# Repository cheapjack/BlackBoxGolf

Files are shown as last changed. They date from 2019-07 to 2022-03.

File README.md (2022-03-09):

# Black Box Golf
Make files, instructions and details of a Science & Technology Studies Crazy Golf hole for [Full Of Noises 2019](http://fonfestival.org/event/full-of-noises-2019-09-11-08-19/) in Barrow Park, Barrow-in-Furness

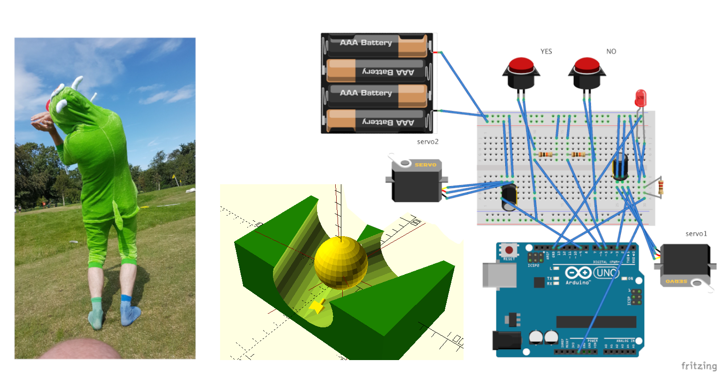
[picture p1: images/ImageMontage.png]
Participant dressed as Euglena, Fritzing Model and 3D CAD for internals


## Premise

Black Boxing is where a very complicated technology (like a computer or a bank) effectively becomes a box hiding how it really works: all we know as black box users is we put something in and expect something to come out. Most of the things we use every day can be seen like this. We thought it would be fun to think about a black box on a golf course.

Science studies is a really useful way of thinking about how science affects society. In Barrow in Furness we can see many ways that science affects our social world; BAE relies on some of the more problematic of scientific developments (weapons & defence) but has a big affect on the local socio-economic world, while many coastal and agricultural sciences have a big role in the town through local industry and agriculture. 

To cite Science Studies scholar Bruno Latour, blackboxing is *"the way scientific and technical work is made invisible by its own success. When a machine runs efficiently, when a matter of fact is settled, one need focus only on its inputs and outputs and not on its internal complexity. Thus, paradoxically, the more science and technology succeed, the more opaque and obscure they become."* <sup>1</sup> 

It's also good at not just thinking about big global science issues but how things work locally. We wanted to use the golf course as a space to think about how hidden non-human creatures like algae live really close to us, despite living in quite a tightly controlled industrial and agricultural environment. Generally we're too busy surviving in our social worlds to stop and think about tiny creatures, but some family time playing crazy golf might be a nice easy way to think about microbiology. Though of course the important thing is to complete your game in as few shots as possible; and if you follow our black box activity instructions carefully we might help you win and learn about the microscopic world of algae and how scientists use model organisms!

A model organism is a non-human species that is extensively studied to understand particular biological phenomena and provide insight into the workings of other more complicated organisms. Once these things are established in science the model organism is a bit like a black box and scientists use them to test things a bit like we might use a sensor to turn on an outdoor security light.

## What the black box does

A player's ball enters a compartment in an acrylic black box from a short run and is held within the structure and only released after the 'success' or 'failure' of a condition. A 'success' triggers the ball's release down another run advantageous to the player's next hole, while a 'fail', releases the ball somewhere not to the players advantage, ie away from the next hole

The success or fail is triggered by 2 physical buttons that a human judge can operate. It is arduino based and will run from a rechargeable 3V-5V USB battery pack

Players act out instructions provided on the box on the day, that fellow players, friends or family judge whether they deserve a `success` or `fail`. They have to be honest or they can cheat; it's up to the players.

The black box can be deployed as a kit for future crazy golf at Barrow Park and the conditional system can change each time.

Like much of the tech we all depend on, this hole promises alot, but ultimately provides very little; obscuring hidden communities of humans and non-humans who maintain the infrastructures they depend on.

***How*** it all works is hidden in the shiny black box and we don't really need to know all the hard work that has gone into it for it to work in our golf game. If you *do* need to know you can find [instructions here](https://github.com/cheapjack/BlackBoxGolf/blob/master/HowToBuild.md)

## Black Box activity

Players judge the true/YES or false/NO button press based on observing algae in specially prepared microfluidic environments on microscope slides using Manu Prakesh's [Foldscopes](https://foldscope.com) made at the [Prakesh Lab](https://web.stanford.edu/group/prakash-lab/cgi-bin/labsite/) for 'frugal science'. It might lead to you dressing up as algae, what we call *"Euglena Cosplay"*

## Euglena Cosplay

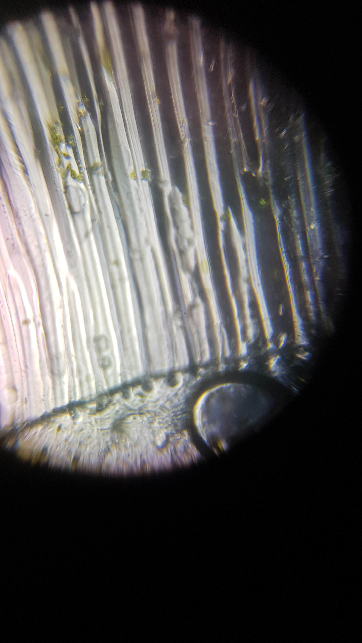
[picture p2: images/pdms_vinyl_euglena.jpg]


Euglena Cosplay is the activity used to self-certify true/YES or false/NO conditions in the black box.

 * Enter golf ball into box
 * Observe Euglena down *Microscope Alley* with pre-prepared [Foldscopes](https://foldscope.com) or failing that on the [model organisms webpage](https://domesticscience.org.uk/criticalkits/euglena.html)
   * They observe Euglena in silicon microfluidic channels moulded from the grooves of Cumbrian charity shop records, a method for model organism observation developed by microbiologist, biotechnologist and engineer [Alexandre Benedetto](https://www.lancaster.ac.uk/health-and-medicine/about-us/people/alexandre-benedetto) inspired by an article in [The Worm Breeders Gazette](http://wbg.wormbook.org/2017/07/18/immobilizing-nematodes-for-live-imaging-using-an-agarose-pad-generated-with-a-vinyl-record/)
    * Wear a Euglena costume and mime their behaviour
    * If you're too embarassed just do mime!
 * Get judged by co-players
 * Hit `true` or `false` buttons
 * Golf ball released:
   * `true`: easy access to next hole
   * `false`: Down a camping stove/ recycled PLA windshield maze

## Cheating

Of course it's up to you to negotiate the complex social world of someone cheating at Crazy Golf; you could choose to do that and ignore our tiny green friends or the brilliant engineerinf behind foldscopes and go straight to a hole-in-one. But you might miss out experiencing some interesting local science techniques.

## How To Build

In quite the opposite spirit to black boxing, read [the basic guide to build it yourself](HowToBuild.md). Arduino abstractions of `C++`, how capacitors, pull up resistors, ground referencing etc work alongwith 300 years of microscopic practice and the physics of ball lenses remain in the black boxes we need them to be in to play this kind of non-human observing crazy golf. 

## References

 * 1. Bruno Latour (1999). Pandora's hope: essays on the reality of science studies. Cambridge, Massachusetts: Harvard University Press. p. 304.

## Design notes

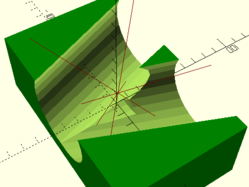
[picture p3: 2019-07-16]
images/Model.png

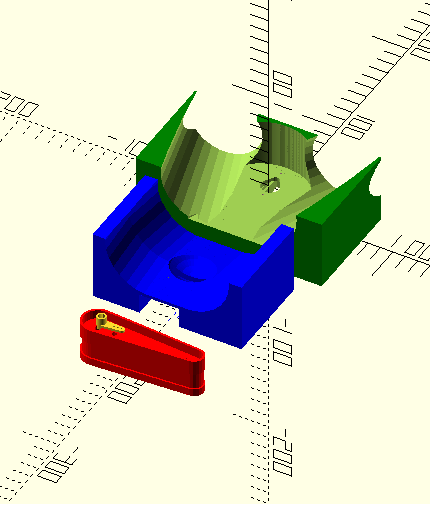
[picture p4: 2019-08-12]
images/model2.png

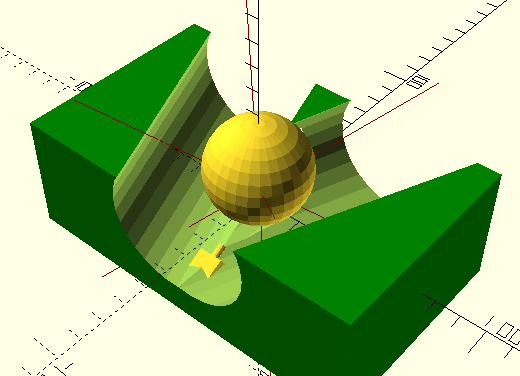
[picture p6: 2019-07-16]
images/blackboxgolfModel.png

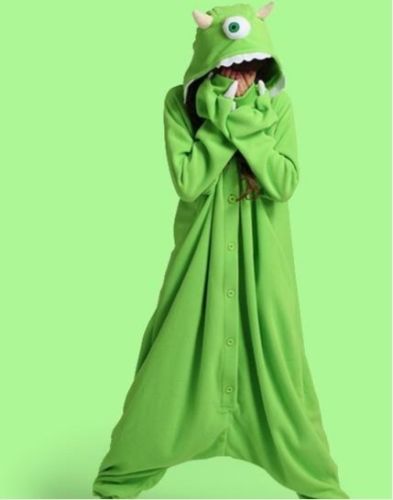
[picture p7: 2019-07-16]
images/mike.jpg

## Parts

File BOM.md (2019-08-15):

### Golf BOM

|No.|Size|Material|Source|Cost(£)|Ordered|Received
|----|----|----|----|----|----|---
1|3-6V|Solenoid|[ebay](#)|4.95|<ul><li>[x] </li>|<ul><li>[x] </li>
2|L/S|Mike Monster<br>Costume|[ebay](#)|35.80|<ul><li>[x] </li>|<ul><li>[x] </li>
2|5V|Hextronik Servo Motors|[ebay](https://www.ebay.co.uk/itm/Hextronik-HXT900-9g-Micro-Servo-1-2-4-Packs-Micro-RC-Planes-Helis-orangeRX-UK/352456068430)|10.99|<ul><li>[x] </li>|<ul><li>[x] </li>
5|2M|Bolt|[ebay](#)||<ul><li>[ ] </li>|<ul><li>[x] </li>
1||Golf Flag|ebay|10.69|<ul><li>[x] </li>|<ul><li>[x] </li>
1||Golf Balls|ebay|12.21|<ul><li>[x] </li>|<ul><li>[x] </li>
1||Folding Camp Deflectors|ebay|10.53|<ul><li>[x] </li>|<ul><li>[x] </li>
1|30ml|Euglena gracilis|[sciento](https://sciento.co.uk)|13.25|<ul><li>[x] </li>|<ul><li>[ ] </li>
1|470uF|Capacitors|amazon|6.99|<ul><li>[x] </li>|<ul><li>[x] </li>
1|UNO|ELEGOO Arduino Compatible R3 Board ATmega328P|[amazon](https://www.amazon.co.uk/gp/product/B01EWOE0UU)|7.99|<ul><li>[x] </li>|<ul><li>[x] </li>
2|AA & AAA|Batteries|Spar Lancaster|6.99|<ul><li>[x] </li>|<ul><li>[x] </li>
20|A5|Instruction Pamphlet|[C3](https://zenithprintgroup.com/c3-imaging/)|20.00|<ul><li>[x] </li>|<ul><li>[x] </li>
1|1000mAh|Solar USB Battery|amazon|18.98|<ul><li>[x] </li>|<ul><li>[ ] </li>
5|600x300mm|Black<br>Acryliv|[Hobarts](https://hobarts.com/3mm-black-cast-acrylic)|42.00|<ul><li>[x] </li>|<ul><li>[x] </li>
||||Total|195.15

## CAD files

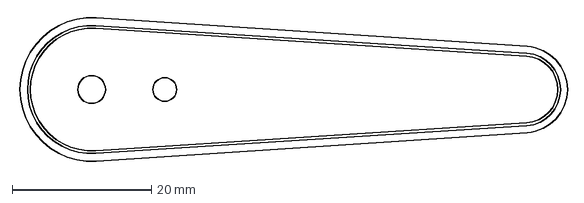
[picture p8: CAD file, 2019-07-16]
builds/flipper/files/flipper_drawings.dxf
79.1 x 21.1 mm

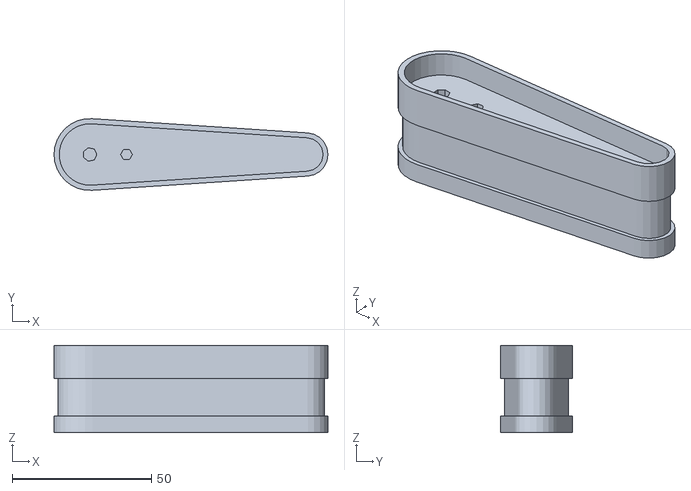
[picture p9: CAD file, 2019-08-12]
builds/Golf_Flipper.stl
98.2 x 25.7 x 31.2

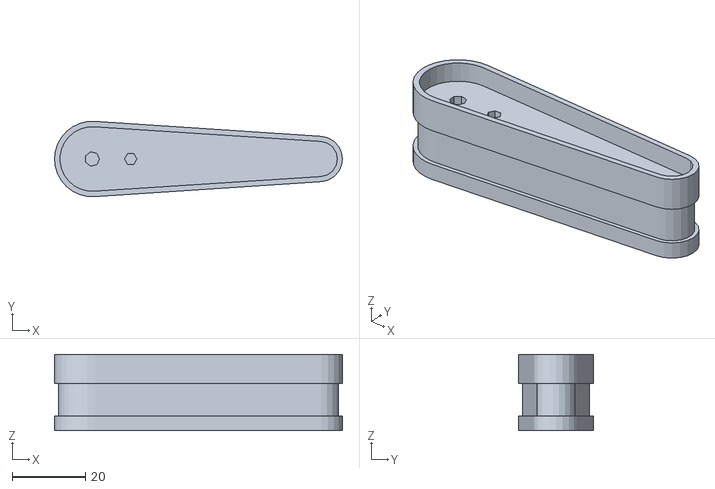
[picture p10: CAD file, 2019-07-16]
builds/flipper/files/flipper.stl
78.6 x 20.5 x 20.8

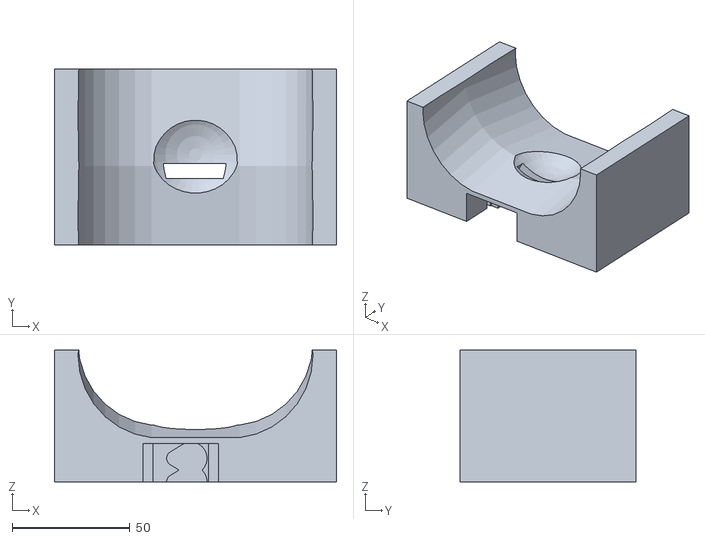
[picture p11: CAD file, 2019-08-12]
builds/Golf_Release_Mechanism.stl
120.0 x 75.0 x 56.0

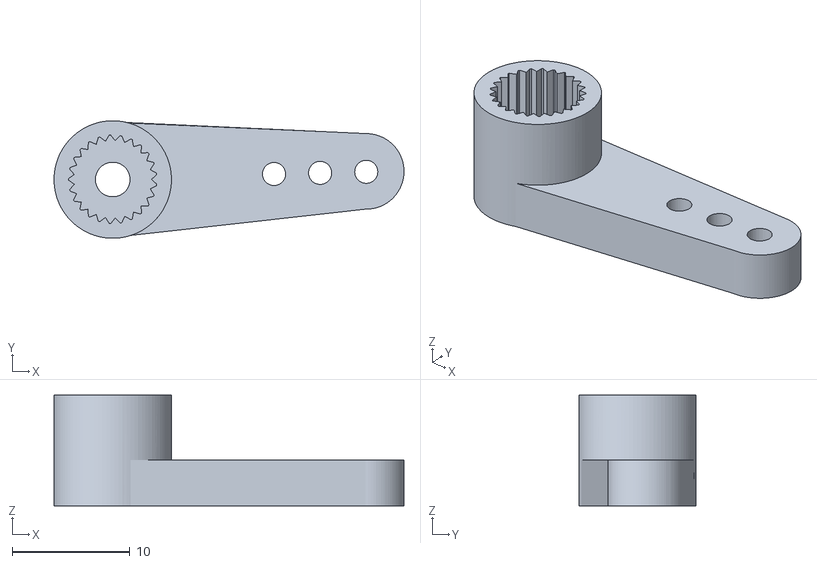
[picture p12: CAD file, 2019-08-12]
builds/servo_arm_merge.stl
29.7 x 9.98 x 9.40

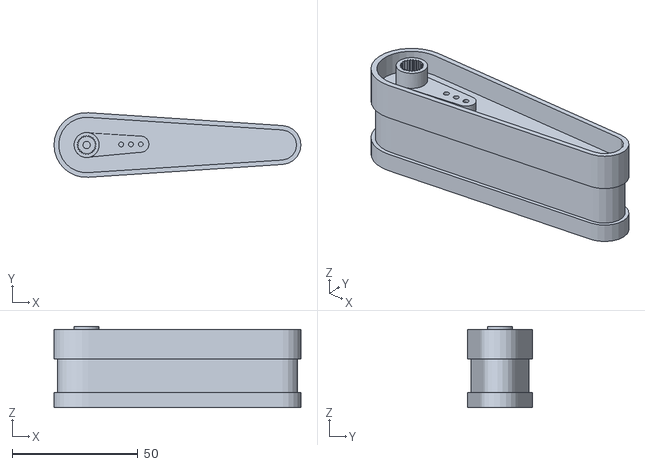
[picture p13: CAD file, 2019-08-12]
builds/Pinball_Adaptor.stl
98.2 x 25.7 x 32.4

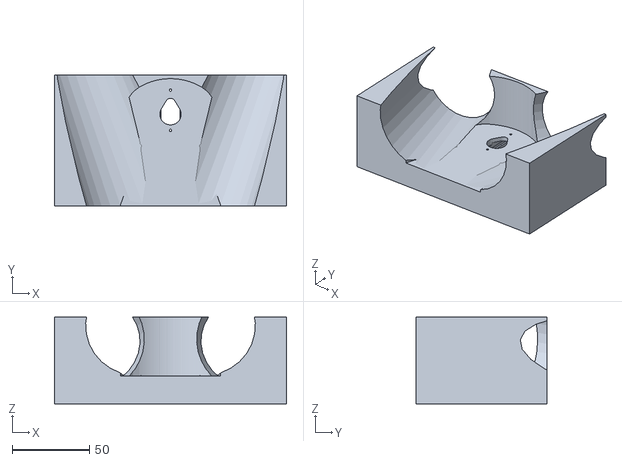
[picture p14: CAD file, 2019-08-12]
builds/Golf_Choice.stl
150.0 x 85.0 x 56.0

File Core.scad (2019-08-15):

// Golf ball official dimensions seem to range from 42.7-41.148mm. We'll round up to 43mm
golfball_diameter=43;
// How much of a rest we want the ball in.
golfball_rest_offset=2;

flipper_recess_scalar=1.25;


servo_width = 12.5;
servo_depth = 23.5;
//includes all the way up to just under the cam assembly
servo_height = 26;
// measure this before printing
servo_pin_height = 11;
servo_pin_depth = 32;
servo_pin_shelf_height = 2.5;
servo_recess_scalar = 1.25;

//servo_arm_scalar = 1.05;
//servo_arm_scalar2 = 1.5;

base_width = 150;
base_depth = 85;
base_height = 76;
//alt height without golf divert overhang
base_height = 56;

short_run_length = base_width/2;

run_opening = 70;
run_leaving = 55;
run_length = 120;
run_angle = 9;
run_level =4;
micro_run_level = -6;
divert_offset = 35;

solenoid_case_width = 12.5;
solenoid_case_depth = 20.5;
solenoid_case_height = 15;//12
solenoid_pin_diameter = 7.5;
solenoid_pin_length = 14;
solenoid_pin_length_retracted = 8;
solenoid_angle = 30;
solenoid_recess_scalar = 1.1;



//////////////////////////////
// Main geometry            //
//////////////////////////////

//translate([0,0,0])print("red");
translate([0,-150,0])print("yellow");
print("green");
print("blue");
//servo_arm(1,1.5);
//translate([-143,-45,22])rotate([0,0,270])servo_arm(1.1,2);
//servo_arm(1.2,1.5);
//translate([-servo_width/2,-135,-18])rotate([90,90,180])servoCase(true);


// print the red, blue or green blocks
module print(state){
    if (state=="red"){
        red();
    } else if (state=="blue"){
        blue();
    } else if (state=="green"){
        green();
    } else if (state=="yellow"){
        yellow();
    } else {
    }
}


// 
// Section 1
// Uncomment when printing

module yellow(){
    color("red")import("builds/Pinball_Adaptor.stl", convexity=3);
}


module green(){
    translate([0,0,base_height/2])difference(){
    mainBox();
    servoPinHoles(-9);
}
}

// a servo for the golf release mechanism
// comment out for building
//translate([-servo_width/2,-135,-18])rotate([90,90,180])servoCase(true);

// a solenoid for the golf release mechanism
//translate([0,-90,-2.26*solenoid_case_height+7])rotate([82,0,0])scale(solenoid_recess_scalar,solenoid_recess_scalar,solenoid_recess_scalar)solenoid(false);

// Section 2
// Uncomment when printing

module blue(){
    translate([0,0,base_height/2])color("blue")setup3();
}

// check for flipper & servo alignment
//color("pink")translate([0,0,0])align_pin(150,3);

// Flipper: uncomment for printing
module red(){
    color("red")translate([0,-200,0])rotate([0,0,0])flipper();
}

module mainBox(){
    translate([0,-15,0])difference(){
        setup1();
        translate([0,21.25,-26])servoCase();
}
}

// Setup for recesses
module setup1(){
    // comment out for build
    //allow for servoCase(); 
    //translate([0,21.25,-25])servoCase();
    // comment out for build
    //translate([0,-100,-20])solenoid();
    section_flipper_recessed();
    //translate([-28,-10,10])golf_ball();
    }

module setup3(){
    difference(){
        release_mechanism();
        translate([-servo_width/2,-135,-18])rotate([90,90,180])servoCase(true);
        // allow void to install servo
        translate([-servo_width/2,-135,-28])rotate([90,90,180])servoCase(true);
        }
        }

module release_mechanism(){
    translate([0,-108,0])difference(){
        section_2(30);
        translate([0,1,14])golf_ball(1.15)translate([-servo_width/2,-135,-18])rotate([90,90,180])servoCase(true);
    }
}


// Pins & Bolt Geometry

// module for checking alignment and M sized fixing
module align_pin(length,diameter){
    rotate([180,0,0])cylinder($fn=24,h=length,r=diameter/2,center=true);
}

// Main section with Base geometry & golf runs removed
module section(){
    difference(){
        base();
        translate([0,0,run_opening/4])divert();
        }
    }

// A section for holding and releasing the ball, iterated cylinders
module section_2(spread){
    difference(){
        base_2();
        rotate([0,0,0])translate([0,-25,28])for (i=[0:spread]){
            translate([i-spread/2,0,0])short_run(i+1);
            }
            }
        }

// section with flipper recess
module section_flipper_recessed(){
        difference(){
            section();
            flipper_recess();
            }
    }
    
// Balls
// average golf ball size
module golf_ball(scale){
    sphere(d=(scale*golfball_diameter) + golfball_rest_offset);
}

// Main Runs Geometry
// 3 cylendrical golfball runs divert true or false
module divert() {
    translate([0,-50,run_level])run();
    rotate([-run_angle,0,0])translate([-divert_offset,0,0])run_true();
    rotate([-run_angle,0,0])translate([divert_offset,0,0])run_false();
}


// Shorter cylinder for golf run with parameters
module short_run(){
    rotate([270+run_angle,0,0])cylinder(h=short_run_length,r=run_opening/2,center=true);
    translate([0,base_depth/2,0])rotate([270-run_angle,0,0])cylinder(h=short_run_length-10,r=run_opening/2,center=true);
   
}

// Basic cylindrical golf run 
module run() {
    rotate([270,0,0])cylinder(h=run_length,r1=run_opening/2,r2=run_leaving/2,center=true);
}

// First bit of the flipper section
module pre_run() {
    rotate([270,0,0])cylinder(h=run_length,r1=run_opening/2,r2=run_leaving/2,center=true);
}

// golf run true direction
module run_true() {
    rotate([0,0,20])run();
    }

// golf run false direction
module run_false() {
    rotate([0,0,-20])run();
    }

// Base Geometrys

// Big chunk o' PLA
module base() {
    color("green")cube([base_width,base_depth,base_height], true);
}

// another base that needs less material
module base_2() {
    color("green")cube([base_width-30,base_depth-10,base_height], true);
}

module base_3() {
    color("green")cube([base_width-30,base_depth-10,base_height], true);
}

// Servo/servo Case

// the main servo case with the cam bits
module servoCase(state){
    //wider pin shelf recess
    translate([0,0,servo_height/2-(servo_pin_height/2)])scale([servo_recess_scalar,servo_recess_scalar,servo_recess_scalar])cube([servo_width,servo_pin_depth, servo_pin_shelf_height], true);
    translate([0,0,-servo_pin_height/6])cube([servo_width,servo_pin_depth,servo_height-(servo_height/8 )], true);
    // Main case
    cube([servo_width,servo_depth,servo_height], true);
    //cam top
    translate([0,servo_depth/-2 + 7.45,servo_height/2+2])scale([servo_recess_scalar,servo_recess_scalar,servo_recess_scalar])servoCamAssembly(11.5,5.25,6,4);
    // a lever left/up if true, otherwise straight
    if (state == true){
        translate([0,servo_depth/-2+6,servo_height/2+8])for (i=[0:180]){
            rotate([0,0,i])servoCamAssembly(7,4,15,4.5);
        }
    } else {
        translate([0,servo_depth/-2+6,servo_height/2+8])servoCamAssembly(7,4,15,4);
    }
}

// The Cam bits
module servoCamAssembly(first_cam_diameter,second_cam_diameter,distance, cam_height){
    //allow for a clean break throught the main box geometry
        linear_extrude(height = cam_height + 2, center = true, convexity = 0, twist = 0)servoCam(first_cam_diameter,second_cam_diameter,distance);
}

// cam hull for the cam top of a servo
module servoCam(first_cam_diameter,second_cam_diameter,distance){
    hull() {
        circle($fn = 24,d = first_cam_diameter);
        translate([0,distance,0])circle($fn = 24,d = second_cam_diameter);
        }
    }
    
// servo attachment pins
module servoPinHoles(ypos) {
    color("pink")translate([0,ypos + 0.6,0])align_pin(50,1.6);
    color("pink")translate([0,ypos + 26.6,6])align_pin(50,1.6);
    // last pin secures flipper and is positioned center of the larger servoCamAssembly hulled circle
    color("pink")translate([0,servo_depth/4-5.75,0])align_pin(75,2);    
}

// Imported Flipper from https://www.thingiverse.com/thing:1789
module flipper(){
    flipper_scalar = 1.25;
    scale([flipper_scalar,flipper_scalar,1.5])import("builds/flipper/files/flipper.stl", convexity=3);
}

//Flipper recess
module flipper_recess(){
    for (i=[330:390])
        translate([0,0,10])rotate([0,0,i])linear_extrude(height = 40, center = true, convexity = 10, twist = 0)hull(i+1) {
        translate([0,-50,0])circle($fn = 24,d = 15);
        translate([0,20,0])circle($fn = 24,d = 40);
        } //resize([flipper_recess_scalar,flipper_recess_scalar,flipper_recess_scalar])import("builds/files/flipper.stl", convexity=3);
}
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

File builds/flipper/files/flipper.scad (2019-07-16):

module outside() {
	union() {
		dxf_linear_extrude(file="flipper_drawings.dxf", layer="outside", height=7.9, convexity=1);
		dxf_linear_extrude(file="flipper_drawings.dxf", layer="setback", height=20, convexity=1);
		translate([0,0,16.8]) {
			dxf_linear_extrude(file="flipper_drawings.dxf", layer="outside", height=4, convexity=1);
		}
	}
}

module inside() {
	union() {
		dxf_linear_extrude(file="flipper_drawings.dxf", layer="cutout", height=4.8, convexity=1);
		dxf_linear_extrude(file="flipper_drawings.dxf", layer="holes", height=16, convexity= 2);
	}
}

translate([-20,0,20.8]) {
	rotate([180,0,0]) {
		difference() {
			outside();
			inside();
		}
	}
}

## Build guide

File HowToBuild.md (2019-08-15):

# How To Build

In quite the opposite spirit to black boxing, here is a basic guide to build it yourself. Arduino abstractions of `C++`, how capacitors, pull up resistors, ground referencing etc work alongwith 300 years of microscopic practice and the physics of ball lenses remain in the black boxes we need them to be in to play this kind of non-human observing crazy golf. 

## Box

We used 3mm Black Acrylic (see [BOM.md](BOM.md) ) to make the box using [MakerCase](https://www.makercase.com/)

We used these [lasercutting design files](https://github.com/cheapjack/BlackBoxGolf/tree/master/box) to cut out a snap fit black acrylic box to fit some nice 3d printed internals. Note the holes in the base for threading through nylon standoffs and spacers, and the Domestic Science logo. You may need to offset the cut paths if your acrylic is not quite 3mm thick by between 0.05-0.1mm depending on your material if you want a snap fit. Hobarts supply pretty consistent thickness, again listed in the [BOM](BOM.md) but you might prefer a local supplier.

We've made 3 artwork sheets in the [sheets directory](https://github.com/cheapjack/BlackBoxGolf/tree/master/box/sheets) that will provide the box and some ramps and internal guides for the battery packs 

## Golf Ball internals

We used the Core.scad file to generate 3 parts using [OpenSCAD](http://www.openscad.org) to make `.stl` files which we then used Cura to generate gcode for an Ultimaker 2+ 3d printer usign 4mm PLA filament on gradual 0-80% infill.

2 Hextronik 9 g Micro Servos push a golf ball out of it's recess once entering the box, and then guide it via a 3d printed modified pinball flipper in a golf run, controlled by arduino, code included in this repo

We drilled holes in the underside of the 3d printed internals/golf runs 5mm offset for 3mm [nylon standoff/spacers](https://www.ebay.co.uk/itm/Nylon-M2-M2-5-M3-Hex-Column-Male-Female-Screw-Nut-Kit-Box-Standoff-Spacers/163465286260). Each M3 standoff included a 15mm threaded bolt, a 4mm nut, a securing 2mm nut and a 20mm high threaded spacer to secure the 3d printed interals, and leave space for a standard 300 hole PCB breadboard and Arduino. The standoffs fitted and secured the arduino between the base of the box and the 3d printed internals.

A standard nylon M3 spacer kit should give you the parts you need to secure internals by threading the main 15mm screw from the underside of the base of the box.

The 3d printed parts sat on the threaded spacers and the nylon gave some flexibility for construction or repair.

## Arduino and Wiring

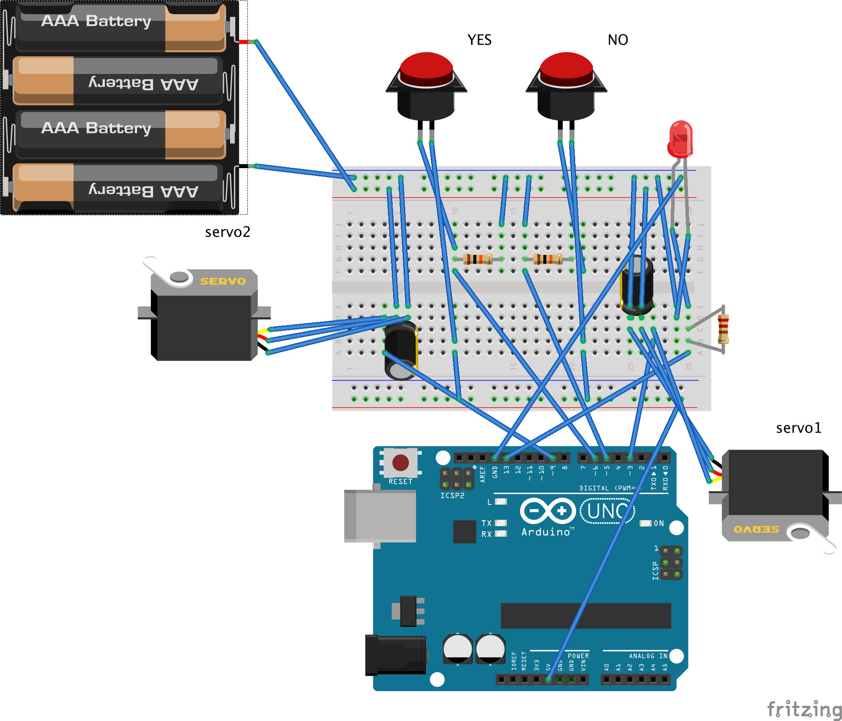
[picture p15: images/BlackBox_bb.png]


2 [Sanwa style arcade buttons](https://www.ebay.co.uk/itm/Genuine-White-Sanwa-SDM-18-Snap-In-Arcade-Button-18mm-Mounting-Hole/392317047559) triggers servos controlled by arduinio standard servo library and also lit up a large 10mm LED to indicate a successful button press. Refer to the Arduino code and wiring diagram provided

We used bell wire to run cabling from the underside of the arcade buttons (soldered on) to the solderless wires on the breadboard and did everything else wiring wise using coloured coded jump wires. The main thing to note is to power the 2 5V servos seperately from the arudino but with a shared ground reference. So 4 x AAA 1.5v batteries is adequate and a 9V battery powers the arduino. These need external on/off switches but we only had time to provide space to access the battery packs. This should be added alongwith a veroboard soldered breadboard or shield for a more robust build. However a solderless breadboard build worked really well.

## Setup and Useage

 * Take the black box and attach a 9V battery to the 9V battery clip on the left of the box
 * Turn the battery pack on the right side on
 * Place the box right by the final hole so the OUT hole on the left will let the golf ball roll into the hole. 
 * Use the silver folding camp stove windshields to capture the ball from the right OUT hole and make a curve so the player has to make several putts to escape
 * Arrange the broken vinyl records to support the black acrylic ramp into the IN hole use the silver gaffa tape to support it
 * Place the ramp, long piece first into the IN hole to guide the ball into the capture zone, a ball shaped cup that the ball falls into when you putt the ball up the ramp. Use the gaffa to secure it.
 * Press the white button to reset the system and green light will flash. Buttons need to be pressed firmly and held for a second then released to register. After 5 second you will hear the internal servos reset to the starting ball capturing positions.
 * You are now ready to play and follow the printed instructions
 * When the ball is captured follow these YouTube instructions on how to see the algae swimming in the record grooves using the paper foldscope microscopes provided. https://youtu.be/VdcvPJWPRNE
   * Basically hold them blue side up and place finger on and thumb around the blue tabs with a semi circular pattern of holes. The video describes it best.
 * Our foldscopes have prepared slides already loaded with algae and their environments. They also have led light packs that help viewing indoors but sunlight is best. Warn young players not to look directly into the sun.
   * They are looking for tiny green tube like creatures swimming in the grooves
   * Don't worry about enforcing wearing costumes! People are quite happy to just mime with their bodies which I think is good enough!
   * Let them decide which button to press!

## Notes

It's worth having someone to help with the scopes and encouraging people how to use it especially if the course gets busy. It's not very stand alone I'm afraid but it's a good way of taking to participants!

## Issues

Sometimes after pressing the black button the internal servo fails to reset into the ball capturing position. This means players can putt the ball straight through and win. This is just good luck on their part! By pressing the white button with no ball present, this seems to reset the servo correctly.

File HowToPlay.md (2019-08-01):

## Black Box Golf

Black Boxing is where a very complicated technology or system (like a computer or a bank) is simplified. In practice much technology we use everyday is more like a box hiding how it works, how it was made and how it might affect other living things: all we know is we put something in and something comes out. Most of the time this doesnt matter but in a complicated world where what we make and how we make it matters maybe we need to wonder what is behind the black boxes we use and what humans and non-humans are part of that.

In this golf hole a classic black box has a space for your decisions based on looking at microscopic algae and the people playing with you.

### Instructions

 * **Putt** the ball into the `IN` hole
  * Your ball will be held inside until you press the black or white button which represent a `success` or `fail`. Even the most elaborate algorithm is not a black box on it's own, but made by people.
 * Have a **look** down the microscopes provided
  * If your microscope does not work or you can't see anything visit `bit.ly/EuglenaSwim`
  * You will **see** tiny algae creatures called *Euglena gracilis* swimming in tiny channels made from the grooves of old vinyl records. This is a lesser known technique used by microbiologists in Lancaster University to observe tiny model organisms. simple creatures that teach biologists about how living things work.
* **Observe** how the creatures behave.
* **Act** out what you oberve with your body. Use the green Euglena Onesies (one Large, one Small) to help you!
 * Get someone playing with you to **judge** how well you do and press the **black** or **white** based on your performance.
 * **PRESS** **black** will send you on a more difficult putting course to the next hole.
 * **PRESS** *white** Will send you to the easy route to the next hole!
 * Thanks for playing!
 * If you want to know how this was made **visit** `github.com/cheapjack/BlackBoxGolf`

## Euglena gracilis

Euglena is a genus of single celled flagellate eukaryotics. Species of Euglena are found in freshwater and salt water. They are often abundant in quiet inland waters where they may bloom in numbers sufficient to color the surface of ponds and ditches green. 

The species we are looking at Euglena gracilis has been used extensively in the laboratory as a model organism. Interestingly they can photosynthesise like plants but can eat and move like animals, with an 'eye pit' to sense light which they move toward, blurring the boundary between plant and animal. 

Today you can see them on specially prepared microscope slides, where they swim around tiny microscopic channels. These channels have been made by pouring silicon into the grooves of vinyl records, a cheap way of isolating individual model organisms of this size and is a technique developed by Alexandre Benedetto a researcher & lecturer at Lancaster University.

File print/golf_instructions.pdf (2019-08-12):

# Black Box Golf

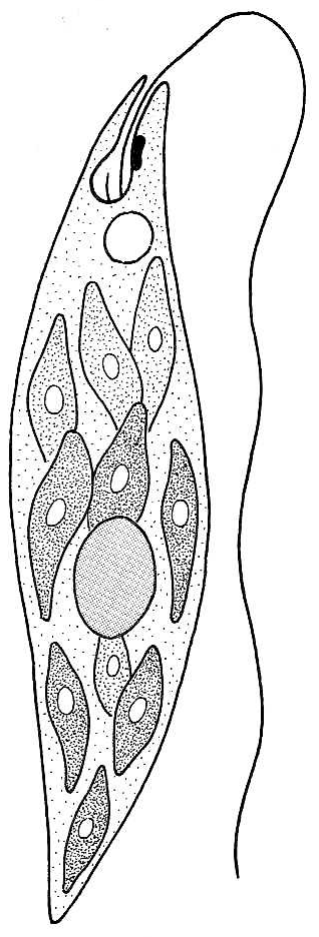
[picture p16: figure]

## Instructions

- PUTT the ball into the In hole
Your ball will be held inside until you press the black or white button which represent a success or fail. Even the most elaborate algorithm is not a black box on it’s own, but made by people.
- Have a LOOK down the microscopes provided.
- If your microscope does not work or you can’t see anything visit bit.ly/EuglenaSwim.
You will see tiny algae creatures called Euglena gracilis swimming in tiny channels made from the grooves of old vinyl records. This is a lesser known technique used by microbiologists in Lancaster University to observe tiny model organisms, simple creatures that teach biologists about how living things work.
- OBSERVE how the creatures behave.
- ACT out what you oberve with your body.
Use the green Euglena Onesies (one Large, one Small) to help you!
- Get someone playing with you to JUDGE how well you do and press the black or white based on your performance.
Pressing black will send you on a more difficult putting course to the next hole. Pressing white will send you to the easy route to the next hole!

Thanks for playing!

If you want to know how this was made visit github.com/cheapjack/BlackBoxGolf

Black Boxing is where a very complicated technology or system (like a computer or a bank) is simplified. In practice much technology we use everyday is more like a box hiding how it works, how it was made and how it might affect other living things: all we know is we put something in and something comes out. Most of the time this doesn’t matter but in a complicated world where what we make and how we make it matters maybe we need to wonder what is behind the black boxes we use and what humans and non-humans are part of that.

In this golf hole a classic black box has a space for your decisions based on looking at microscopic algae and the people playing with you.

Euglena gracilis
Euglena is a genus of single celled flagellate eukaryotics. Species of Euglena are found in freshwater and salt water. They are often abundant in quiet inland waters where they may bloom in numbers sufficient to colour the surface of ponds and ditches green.

The species we are looking at Euglena gracilis has been used extensively in the laboratory as a model organism. Interestingly they can photosynthesise like plants but can eat and move like animals, with an ‘eye pit’ to sense light which they move toward, blurring the boundary between plant and animal.

Today you can see them on specially prepared microscope slides, where they swim around tiny microscopic channels. These channels have been made by pouring silicon into the grooves of vinyl records, a cheap way of isolating individual model organisms of this size and is a technique developed by Alexandre Benedetto, a researcher & lecturer at Lancaster University.

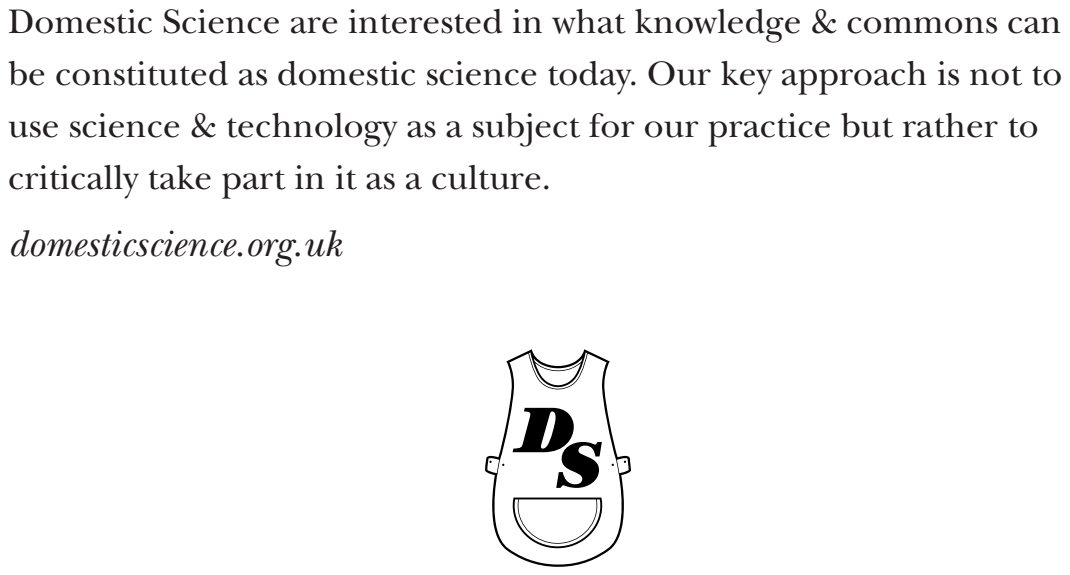
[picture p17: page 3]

Domestic Science are interested in what knowledge & commons can
be constituted as domestic science today. Our key approach is not to
use science & technology as a subject for our practice but rather to
critically take part in it as a culture.
domesticscience.org.uk

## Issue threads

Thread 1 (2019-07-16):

Update the Bill of Materials

cheapjack, 2019-07-16:
### Golf BOM

|No.|Size|Material|Source|Cost(£)|Ordered|Received
|----|----|----|----|----|----|---
1|3-6V|Solenoid|[ebay](https://www.ebay.co.uk/itm/3-6V-Mini-DC-Solenoid-Electromagnet-Push-Pull-Through-Type-Electric-Magnet/223507062533)|4.95|<ul><li>[x] </li>|<ul><li>[x] </li>
1|4.5V|40g/3mm <br>Push Pull Solenoid|[ebay](https://www.ebay.co.uk/itm/DC-4-5V-40g-3mm-Open-Frame-Actuator-Push-Pull-Solenoid-Electromagnet-H227/113761237532)|5.99|<ul><li>[x] </li>|<ul><li>[ ] </li>
2|L&S|Unisex Adult Kigurumi<br>Animal Cosplay Costume|[ebay](https://www.ebay.co.uk/itm/Unisex-Adult-Kigurumi-Animal-Cosplay-Costume-Pajamas-Onesie17-Sleepwear-Outfit/283523416377)|35.80|<ul><li>[x] </li>|<ul><li>[x] </li>
1|3~6V|Hextronik HXT900 9g Micro Servo Motor|[ebay](https://www.ebay.co.uk/itm/Hextronik-HXT900-9g-Micro-Servo-1-2-4-Packs-Micro-RC-Planes-Helis-orangeRX-UK/352456068430)|6.99|<ul><li>[x] </li>|<ul><li>[x] </li>
1||Bubble Machine|Poundland|1.50|<ul><li>[x] </li>|<ul><li>[x] </li>
1||Stove Windshield|[ebay](https://www.ebay.co.uk/itm/9-Plates-Wind-Deflectors-Foldable-Outdoor-Camping-Gas-Stove-Wind-Shield-Scre-ST/133103474756)|10.53|<ul><li>[x] </li>|<ul><li>[x] </li>
3||Golf Balls|[ebay](https://www.ebay.co.uk/itm/White-Fluorescence-Light-up-Luminous-Night-light-Glowing-Golf-Ball-In-UK/163770987322)|12.21|<ul><li>[x] </li>|<ul><li>[x] </li>
2|3~6V|Hextronik HXT900 9g Micro Servo Motor|[ebay](https://www.ebay.co.uk/itm/Hextronik-HXT900-9g-Micro-Servo-1-2-4-Packs-Micro-RC-Planes-Helis-orangeRX-UK/352456068430)|10.99|<ul><li>[x] </li>|<ul><li>[ ] </li>
5|600 x 300 mm|Black Acrylic|[Hobarts](https://hobarts.com/3mm-black-cast-acrylic)|27.60|<ul><li>[x] </li>|<ul><li>[ ] </li>
5|2M|Bolt|[ebay](#)|5.00|<ul><li>[ ] </li>|<ul><li>[ ] </li>
4|500mm|Pipe Work|[ebay](#)|4.95|<ul><li>[ ] </li>|<ul><li>[ ] </li>
1||Golf Flag|[ebay](https://www.ebay.co.uk/itm/Backyard-Practice-Golf-Hole-Pole-Cup-Flag-Stick-Putting-Green-Flagstick-Sign-Kit/183821993380)|10.99|<ul><li>[x] </li>|<ul><li>[ ] </li>
1||Golf ball run|||<ul><li>[ ] </li>|<ul><li>[ ] </li>
1||Tent Pegs|||<ul><li>[ ] </li>|<ul><li>[ ] </li>
1||FON Storage Box|||<ul><li>[ ] </li>|<ul><li>[ ] </li>
||||Total|£137.41|

Closed 2019-08-12.

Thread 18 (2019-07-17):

Design & Make the button mechanisms

cheapjack, 2019-07-17:
include

- [ ] MoT Buttons modified
- [ ] Cut 2 new black boxes for the MoT button?
- [ ] 1 new modded black box with 2 buttons and a golf hole
- [ ] New green light up button like the [original]()

Closed 2019-07-27.

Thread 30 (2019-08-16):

Modify the pinball flipper with a rotating spring loaded half cup to catch the ball

cheapjack, 2019-08-16:
Quite often the balls velocity allows it to bypass the capture recess, a spring load rotating 'cup' could capture more firmly but rotate away when the flipper activates

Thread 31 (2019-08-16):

Troubleshoot the servo angle errors

cheapjack, 2019-08-16:
After triggering the NO button, the servo fails to fully return to the 90 degree position. work out why this is happening and adjust the code, or replace the servo

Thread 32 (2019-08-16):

Reconsider the cosplay element

cheapjack, 2019-08-16:
People generally dont like dressing up in public too much and this performance approach is a bit too theatrical for the Domestic Science approach. It gets in the way of people enjoying discovering the algae with Foldscopes and understanding the PDMS moulding method.

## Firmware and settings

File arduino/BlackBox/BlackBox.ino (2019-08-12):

////////////////////////////////////////////////
// Toggle a black box to choose left or right //
// Golf ball movements                        //
// https://github.com/cheapjack/BlackBoxGolf/ //
//                                            //
//                                            //
////////////////////////////////////////////////

#include <Servo.h>
const int button = 6; //button pin, connect to ground to move servo
const int buttonNo = 5; //button pin, connect to ground to move servo
int pressYes = 0;
int pressNo = 0;
int decision = 0;
Servo servo;
Servo servo2;
boolean toggle = true;
boolean toggleNo = true;
boolean released = false;
boolean noReleased = false;
//boolean flag = false;
const int ledPin =  13;      // the number of the LED pin
const int Servo1OnAngle = 160;
const int Servo1OffAngle = 20; // Angle to default to
const int Servo2RightAngle = 108;
const int Servo2LeftAngle = 50;
const int Servo2OffAngle = 90; // Angle to default to

void setup()
{
  Serial.begin(9600);
  pinMode(button, INPUT); //arduino monitor pin state
  pinMode(ledPin, OUTPUT);
  servo.attach(9); //pin for servo control signal
  servo2.attach(3); //pin for servo control signal
  digitalWrite(5, HIGH); //enable pullups to make pin high
  servo.write(Servo1OffAngle);
  //delay(15);
  servo2.write(Servo2OffAngle);
  //delay(15);
  Serial.println("Button Pressed Yet?");
  digitalWrite(ledPin, LOW);

}

void loop()
{
  Serial.println("Looking at Buttons...");
  pressYes = digitalRead(button);
  delay(10);
  pressNo = digitalRead(buttonNo);
  if (pressYes == HIGH && pressNo == LOW)
  {
    if(toggle)
    {
      Serial.println("Yes Pressed");
      digitalWrite(ledPin, HIGH);
      servo2.write(Servo2RightAngle);
      delay(20);
      servo.write(Servo1OnAngle);
      delay(15);
      toggle = !toggle;
      released = true;
      Serial.print(released);
      Serial.println("Golf ball on it's way to the right!");
      delay(5000);
      Serial.print("Resetting");
      servo2.write(Servo2OffAngle);
      delay(20);
      servo.write(Servo1OffAngle);
      delay(15);
      digitalWrite(ledPin, LOW);
    }
  }
    else if (pressNo == HIGH && pressYes == LOW)
    {
      if(toggleNo)
      {
        Serial.println("No Pressed!");
        digitalWrite(ledPin, HIGH);
        delay(50);
        digitalWrite(ledPin, LOW);
        delay(30);
        digitalWrite(ledPin, HIGH);
        delay(50);
        servo2.write(Servo2LeftAngle);
        delay(20);
        servo.write(Servo1OnAngle);
        delay(15);
        toggleNo = !toggleNo;
        noReleased = true;
        Serial.println("noReleased state:");
        Serial.print(noReleased);
        Serial.println("Golf ball on it's way to the left!");
        delay(5000);
        Serial.print("Resetting");
        servo2.write(Servo2OffAngle);
        delay(20);
        servo.write(Servo1OffAngle);
        delay(15);
        digitalWrite(ledPin, LOW);
        }
    } 
    else
    {
      digitalWrite(ledPin, LOW);
      servo.write(Servo1OffAngle);
      delay(15);
      servo2.write(Servo2OffAngle);
      delay(15);
      toggle = !toggle;
      toggleNo = !toggleNo;
      released = !released;
      noReleased = !noReleased;
      Serial.println(released);
      }
      delay(500);  //delay for debounce
  }

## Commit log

2019-07-16 Added materials so far
2019-07-16 Updated BOM
2019-07-17 Updated mechanism
    [Core.scad]
2019-07-18 Added documentation and images
    [Core.scad]
2019-08-01 Added some detail about the Euglena and the OpenSCAD 3d print files
    [Core.scad]
2019-08-12 updated the BOM and latest 3d print build Core.scad
    [Core.scad]
2019-08-12 Added the box cut files and sheets for 600x300 mm black acrylic
2019-08-12 Added the stl files exported from Core.scad for 3d printing
    [Golf_Choice.stl, Golf_Flipper.stl, Golf_Release_Mechanism.stl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]
2019-08-12 updated the BOM total
2019-08-12 added arduino code and a How to guide
2019-08-12 Added wiring diagram
2019-08-15 Updated Core
    [Core.scad]
